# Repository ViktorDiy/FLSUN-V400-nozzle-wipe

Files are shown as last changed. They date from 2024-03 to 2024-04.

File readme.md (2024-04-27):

It really can save a lot of time...</br>
https://www.facebook.com/100094217897627/videos/2682152451932166/ </br>
</br>
For this setup you need:</br>
- x1 M4 20mm screw </br>
- x2 M4 nut</br>
- x2 bearing 624 ZZ or another wiht 4mm inner diameter, 13mm outer diameter and 5mm width</br>
- x1 MG90S Metal Gear Servo Micro like this - https://www.aliexpress.com/item/1005005464117939.html</br>
- x1 metal brush like this - https://www.aliexpress.com/item/1005004449962700.html</br>
</br>
First step - you should print 3 parts from STL files - base, arm and bucket. It was developed for limited printer space for most popular enclosure in internet - https://www.printables.com/fr/model/323012-flsun-v400-enclosure-cut-abs-version </br>
</br>
It will be usefull to read about this nozzel wiper for Voron 3d printer: https://github.com/VoronDesign/VoronUsers/tree/main/printer_mods/chirpy/NozzleWiper</br>
</br>
Usually you can connect your PWM servo pin via BLTOUCH PWM pin on 3d printer MCU (PA8 for FLSUN castrated clone of MKS Robin nano v2), but after failure try I find 
out that on this pin I have non standard PWM signal, but heart attack cardiogram )))</br>
</br>
I connected PWM servo pin to E1 STEP pin PD15 and power to BLTOUCH GND and +5V or you can cinnect it to any empty 3pin slots:</br>

 </br>

Setup jumpers for STEP/DIR mode:</br>

 </br>
MG90S servo pinout:</br>

 </br>

Assembled rotation part:</br>

 </br>

I used this type of servo arrow arm:</br>

 </br>

Assembled parts in middle arm position of servo should be very close to enclosure wall:</br>

 </br>

Then you should add to your printer.cfg file string [include nozzlewiper.cfg]. </br>
</br>
And download to your printer configuration folder example file nozzlewiper.cfg</br>
</br>
After save and restar on printer dashbord will appear nozzel wiper macro with prefix "NW".</br>
</br>
Befor first use you should calibrate initial/parking position angle of arm and working position angle (minimum_pulse_width: for 0 arm angle and maximum_pulse_width: for
180 angle).</br>
I use command line on dashboard for that. I try to find by command "SET_SERVO SERVO=wipeServo WIDTH=0.001" number when arm doesn't move after WIDTH decrease and the same
command wiht WIDTH increase for maximum angle.</br>
Then you should find by this command volumes for parking position angle and wiping position angle. Wiping position angle of arm should be 90 degree angle between arm
and Xaxis (front/face of printer).</br>
</br>
And you should find nozzle position under center of the backet. You should move printer head manualy to nozzel position under center of the backet and 1-2 mm lower
than metal brash.</br>
You should write this X,Y,Z volumes to nozzelwiper.cfg file.</br>

How I use this setup... How I configured it...

I put macroses from nozzelwiper.cfg to slicer Machine start G-CODE and it looks like:</br>
</br>
G21</br>
G90</br>
M82</br>
G28</br>
NW_DEPLOY</br>
M107 T0</br>
M140 S[bed_temperature_initial_layer_single]</br>
M104 S[nozzle_temperature_initial_layer] T0</br>
M190 S[bed_temperature_initial_layer_single]</br>
M109 S[nozzle_temperature_initial_layer] T0</br>
NW_WIPE</br>
NW_RETRACT</br>
G1 F3000 Z1</br>
G1 X-150 Y0 Z0.4</br>
G92 E0</br>
G3 X0 Y-130 I150 Z0.3 E30 F2000</br>
G92 E0</br>
</br>

</br>
</br>
Befor start of heating nozzle and plate bucked should move to wiping position and nozzel to the center under the bucket. During nozzel and plate heating waste filament from nozzel will drop to the bucket. After nozzel and plate heating nozzel will be wiped by metal brush. </br>
And then printing will start as usual )))

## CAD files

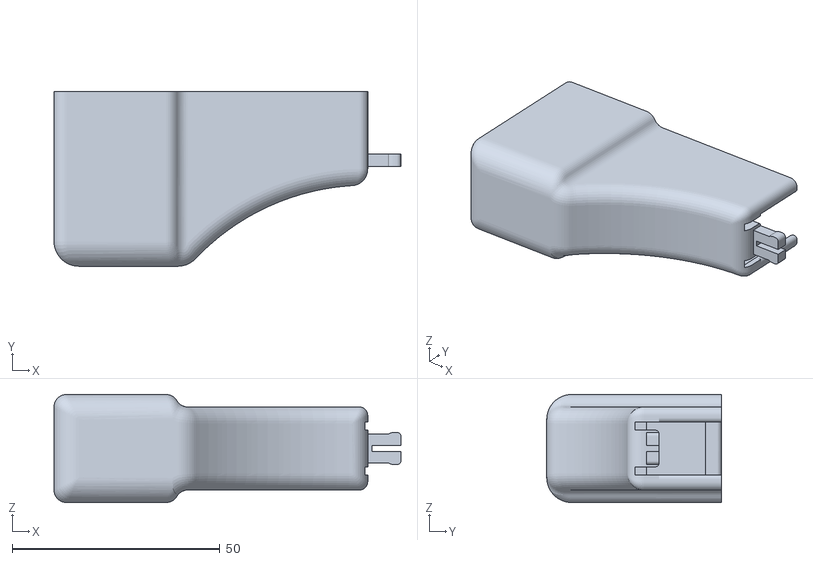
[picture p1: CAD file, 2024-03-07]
Bucket King Size.STL
83.5 x 42.0 x 26.0

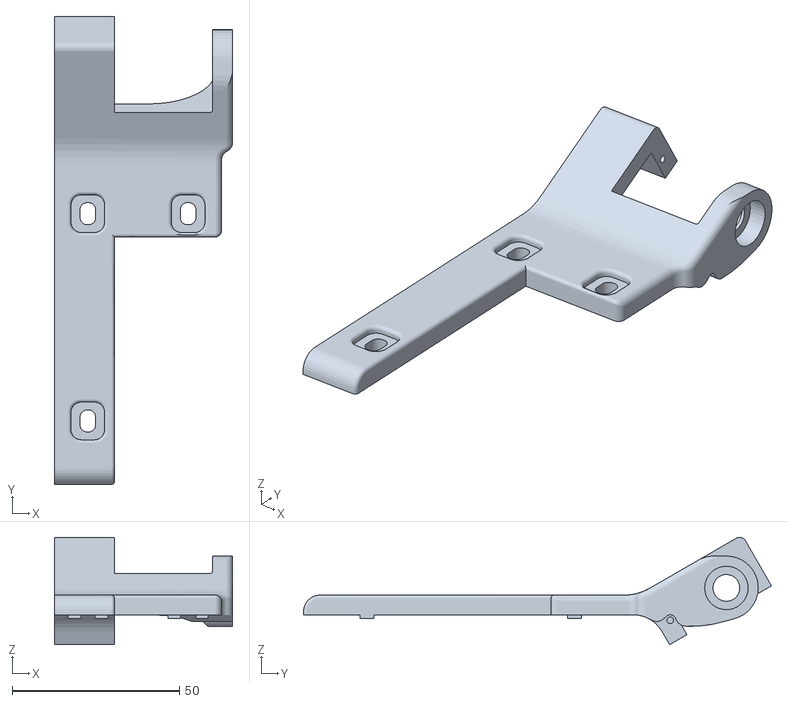
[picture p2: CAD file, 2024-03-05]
Base.STL
53.3 x 140.0 x 32.1

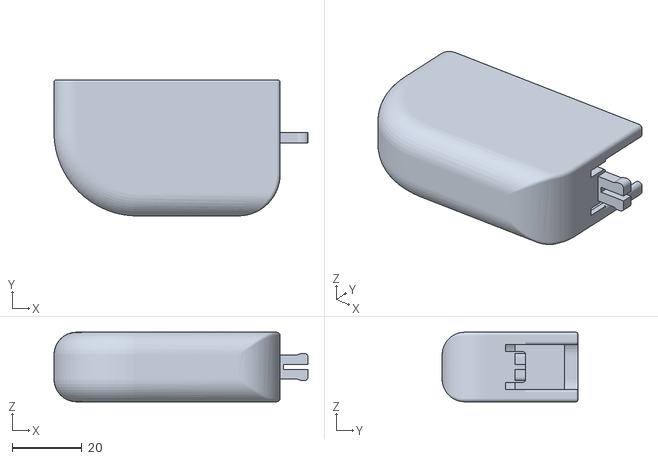
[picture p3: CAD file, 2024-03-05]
Bucket.STL
73.0 x 39.0 x 20.0

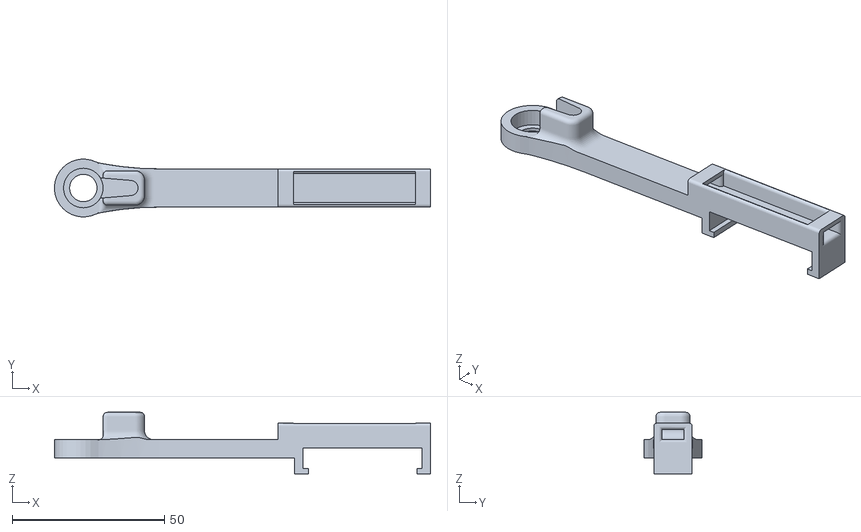
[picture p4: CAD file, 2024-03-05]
Arm.STL
123.5 x 18.9 x 20.2

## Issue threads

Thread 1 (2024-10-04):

Setup jumpers for STEP/DIR mode

chaffoke, 2024-10-04:
Hi,
I have almost everything to install it on my v400 (only bearings missing) ans inwas wondering what do you mean with "Setup jumpers for STEP/DIR mode" ??

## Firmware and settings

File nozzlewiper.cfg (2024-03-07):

[servo nservo]
pin: PD15 #E1 STEP pin
minimum_pulse_width: 0.0005
maximum_pulse_width: 0.0022
maximum_servo_angle: 180
initial_pulse_width: 0.0014   #parking position

[gcode_macro NW_BUCKET_POS]
# Sensible values for variable_x would be 0, but adjust as per the instructions
variable_x: -71.12
# Sensible values for variable_y would be around 90, but adjust as per the instructions
variable_y: 83.25
# Sensible value for variable_z is 50
variable_z: 49.312
gcode:
  M118 bucket pos X:{printer["gcode_macro NW_BUCKET_POS"].x} Y:{printer["gcode_macro NW_BUCKET_POS"].y} Z:{printer["gcode_macro NW_BUCKET_POS"].z}

[gcode_macro NW_DEPLOY] #move bucket to wiping position and nozzel to the center of bucket
gcode:
    G90
    SET_SERVO SERVO=nservo WIDTH=0.00204 #wiping position angle
    G0 Z{printer["gcode_macro NW_BUCKET_POS"].z + 100}
    G0 X{printer["gcode_macro NW_BUCKET_POS"].x}
    G0 Y{printer["gcode_macro NW_BUCKET_POS"].y}
    G0 Z{printer["gcode_macro NW_BUCKET_POS"].z}
    G4 P500
    
[gcode_macro NW_RETRACT] #return arm to parking
gcode:
    SET_SERVO SERVO=nservo WIDTH=0.0014 #parking position
    G4 P500

[gcode_macro NW_WIPE] #move nozzel under metal brush
gcode:
    G90
    G0 Y{printer["gcode_macro NW_BUCKET_POS"].y + 45}
    G0 Y{printer["gcode_macro NW_BUCKET_POS"].y}
    G0 Y{printer["gcode_macro NW_BUCKET_POS"].y + 45}
    G0 Y{printer["gcode_macro NW_BUCKET_POS"].y}
    G0 Y{printer["gcode_macro NW_BUCKET_POS"].y + 45}
    G0 Y{printer["gcode_macro NW_BUCKET_POS"].y}
    G0 Y{printer["gcode_macro NW_BUCKET_POS"].y + 40}
